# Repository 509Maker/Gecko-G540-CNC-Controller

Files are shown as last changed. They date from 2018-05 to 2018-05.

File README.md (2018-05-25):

# Gecko G540 CNC Controller
***
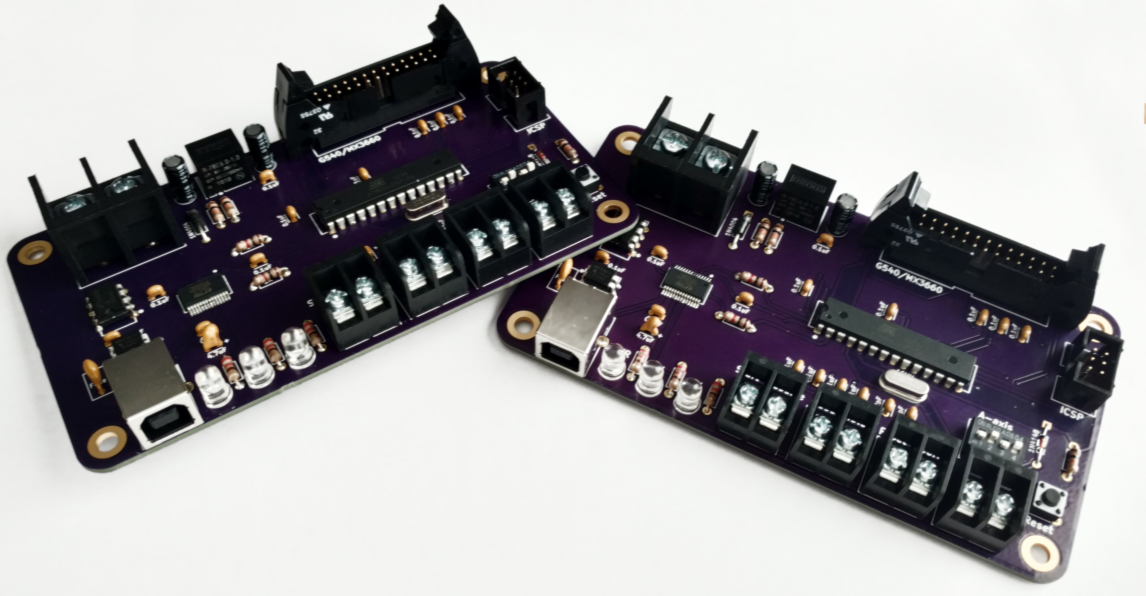
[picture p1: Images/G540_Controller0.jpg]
G540 Controller


#### Don’t be held back by a parallel port!

***

509Maker’s G540 USB CNC Controller is designed to be a plug and play solution for your G540 driver when using the GRBL or Estlcam firmware. 

* [GRBL](https://github.com/gnea/grbl) : Grbl is free software, released under the GPLv3 license.
* [Estlcam](https://www.estlcam.de/) : Affordable Windows Cam / Control software.

***
## Controller Overview

* Compatable with Estlcam and GRBL Latest releases.
* [custom Optiboot Bootloader](https://github.com/509Maker/Optiboot-for-grbl) : that disables D13 from toggling during a power cycle. 
* Authentic FTDI FT232RL USB bridge
* Atmega328P core processor
* ICSP header for atmega328p
* IDC26 header for direct connection to Gecko G540 driver
* Screw terminals for Start/Resume , Feed/Hold , Reset/Abort and Mist Coolant (Pin A4)
* On board dip switch to select what axis gecko clones on A-axis (X or Y)
* Power , RX and TX on board LED status indicators
* On board 5v 1A Recom regulator
* Board can be powered over USB or external source
* 7-24V External power source input screw terminals
* Limit switches , touch probe , spindle and coolant relays make full use of Opto-isolators through the Gecko built in G540 break out board.

The G540 usb CNC Controller when running the latest revision of GRBL is compatible with a number of cross platform control software. Such as GRBL Panel, Bcnc, universal G-code Sender just to name a few!

* [Bcnc](https://github.com/vlachoudis/bCNC) 
* [UGS](https://winder.github.io/ugs_website/) 
* [GRBL Panel](https://github.com/gerritv/Grbl-Panel) 

***

### Required GRBL Complie Time Options

* #define ENABLE_M7  By Uncommenting this line you can use the additinal onboard output labeled A4 for Mist Coolant. 
* #define USE_SPINDLE_DIR_AS_ENABLE_PIN This will need to be uncommented due to the controllers IDC26 Header pinout. 

As you will see in the grbl config.h file the defualt behavior of Optiboot to toggle pin D13 during a power cycle can cause issues ( unintentional spindle start). Please see above; as you will need to use our updated bootloader to rectify this potential problem. Like wise you can choose to not run a bootloader and load grbl via a programmer. It is reccomended to use the custom Optiboot bootloader to allow easy and quick updates over USB. 

***

### Best Way To Show Support For My Work

* [Shop On Amazon](https://amzn.to/2LtLY6S) : If you are in the U.S.A you can use my amazon affiliate link to do your regular amazon shoping at no additinal cost to you ! I recive a small amount when items are purchased through my link. 
* [Paypal Donations](https://www.paypal.com) : Can be sent to Contact@509maker.com
* [Blank PCB](https://www.509maker.com/product/pcb-cnc-controller/) : From time to time I will have blank cnc controller pcb's avalible in single quantity. Boards are made by Oshpark. When you only need one board and want to support the designer it is a great choice. 

# Thank You

No matter how you support my work, from any of the above to sharing your builds and projects with me and on social media platforms. Thank you ! I appreciate it. 

***

### License 

CC BY-NC 4.0

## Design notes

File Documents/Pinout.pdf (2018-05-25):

LPT IDC26 / DB25 | CONNECTION | IMPLEMENTED USE
1 | Output | Spindle On / Off Signal
2 | X-axis Step
3 | X-axis Dir
4 | Y-axis Step
5 | Y-axis Dir
6 | Z-axis Step
7 | Z-axis Dir
8 | A-axis Step | Clone Y-axis Step
9 | A-axis Dir | Clone Y-axis Dir
10 | Input | X-axis Limit/Home Switch Signal
11 | Input | Y-axis Limit/Home Switch Signal
12 | Input | Z-axis Limit/Home Switch Signal
13 | Input | Tool Probe / Touch Off Plate Signal
14 | PWM | Spindle Speed PWM Signal
15 | Not Used
16 | Not Used
17 | Output | Coolant On / Off Signal
18 | GND
19 | GND
20 | GND
21 | GND
22 | GND
23 | GND
24 | GND
25 | GND
26 | Not Used

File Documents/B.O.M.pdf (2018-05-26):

# Gecko G540 CNC Controller B.O.M

Quantity | Part | Digikey Source | Digikey Price | Amazon Option
1 | ATMEGA328P-PU | ATMEGA328P-PU-ND (https://www.digikey.com/product-detail/en/microchip-technology/ATMEGA328P-PU/ATMEGA328P-PU-ND/1914589) | $2.14 | ATMEGA328P (https://amzn.to/2xfAS1Z)
1 | FT232RL-REEL | 768-1007-1-ND (https://www.digikey.com/product-detail/en/ftdi-future-technology-devices-international-ltd/FT232RL-REEL/768-1007-1-ND/1836402) | $4.50
1 | LM358AN | LM358ANFS-ND (https://www.digikey.com/product-detail/en/on-semiconductor/LM358AN/LM358ANFS-ND/458690) | $0.50 | LM358AN (https://amzn.to/2KY8kw6)
1 | IRFD9014PBF | IRFD9014PBF-ND (https://www.digikey.com/product-detail/en/vishay-siliconix/IRFD9014PBF/IRFD9014PBF-ND/812475) | $1.02 | IRFD9014PBF (https://amzn.to/2LtWfjc)
1 | USB-B1HSB6 | ED2983-ND (https://www.digikey.com/product-detail/en/on-shore-technology-inc/USB-B1HSB6/ED2983-ND/2677744) | $0.58 | USB-B (https://amzn.to/2J8uOxa)
1 | XG4A-2632 | OR1094-ND (https://www.digikey.com/product-detail/en/omron-electronics-inc-emc-div/XG4A-2632/OR1094-ND/1829320) | $1.70 | XG4A-2632 (https://amzn.to/2IQoxXq)
1 | 30306-6002HB | 3M15451-ND (https://www.digikey.com/product-detail/en/3m/30306-6002HB/3M15451-ND/1237391) | $0.64 | IDC-Header (https://amzn.to/2LtSCK9)
1 | OSTYK55102030 | ED2926-ND (https://www.digikey.com/product-detail/en/on-shore-technology-inc/OSTYK55102030/ED2926-ND/2605215) | $1.34
4 | OSTYK22102030 | ED2958-ND (https://www.digikey.com/product-detail/en/on-shore-technology-inc/OSTYK22102030/ED2958-ND/1588708) | $1.05 | Barrier-Block (https://amzn.to/2IPJa2a)
1 | 1825057-3 | 450-1364-ND (https://www.digikey.com/product-detail/en/te-connectivity-alcoswitch-switches/1825057-3/450-1364-ND/969174) | $0.88 | Dip-Switch (https://amzn.to/2LzqTIe)
1 | 1825910-6 | 450-1650-ND (https://www.digikey.com/product-detail/en/te-connectivity-alcoswitch-switches/1825910-6/450-1650-ND/1632536) | $0.10 | 1825910-6 (https://amzn.to/2LyTRI8)
1 | ATS16A-E | CTX1084-ND (https://www.digikey.com/product-detail/en/cts-frequency-controls/ATS16A-E/CTX1084-ND/2640062) | $0.36 | 16MHz-Crystal (https://amzn.to/2J8Mrgb)
1 | R-78E5.0-1.0 | 945-2201-ND (https://www.digikey.com/product-detail/en/recom-power/R-78E5.0-1.0/945-2201-ND/4930585) | $3.26 | R-78E5.0-1.0 (https://amzn.to/2xf33hA)
1 | RHEF050 | RHEF050HF-ND (https://www.digikey.com/product-detail/en/littelfuse-inc/RHEF050/RHEF050HF-ND/5130260) | $0.55 | Fuse (https://amzn.to/2GRt9qL)
2 | UKL1H100KDDANA | UKL1H100KDDANA-ND (https://www.digikey.com/product-detail/en/nichicon/UKL1H100KDDANA/UKL1H100KDDANA-ND/2428102) | $0.50 | UKL1H100KDDANA (https://amzn.to/2KXuiPS)
1 | C503B-RCN-CW0Z0AA1 | C503B-RCN-CW0Z0AA1-ND (https://www.digikey.com/product-detail/en/cree-inc/C503B-RCN-CW0Z0AA1/C503B-RCN-CW0Z0AA1-ND/1922930) | $0.15 | Red-Led (https://amzn.to/2IQrRBS)
1 | C503B-GAN-CB0F0791 | C503B-GAN-CB0F0791-ND (https://www.digikey.com/product-detail/en/cree-inc/C503B-GAN-CB0F0791/C503B-GAN-CB0F0791-ND/1922938) | $0.24 | Green-Led (https://amzn.to/2KZ4McP)
1 | C503B-AAN-CY0B0251 | C503B-AAN-CY0B0251-ND (https://www.digikey.com/product-detail/en/cree-inc/C503B-AAN-CY0B0251/C503B-AAN-CY0B0251-ND/1922932) | $0.15 | Amber-Led (https://amzn.to/2kr9kxB)
3 | CF14JT220R | CF14JT220RCT-ND (https://www.digikey.com/product-detail/en/stackpole-electronics-inc/CF14JT220R/CF14JT220RCT-ND/1830334) | $0.10 | CF14JT220R (https://amzn.to/2IQgo5p)
3 | CF14JT10K0 | CF14JT10K0CT-ND (https://www.digikey.com/product-detail/en/stackpole-electronics-inc/CF14JT10K0/CF14JT10K0CT-ND/1830374) | $0.10 | CF14JT10K0 (https://amzn.to/2ktRIBk)
2 | CF14JT1K00 | CF14JT1K00CT-ND (https://www.digikey.com/product-detail/en/stackpole-electronics-inc/CF14JT1K00/CF14JT1K00CT-ND/1830350) | $0.10 | CF14JT1K00 (https://amzn.to/2J4WRh7)
14 | C320C104K5R5TA | 399-4264-ND (https://www.digikey.com/product-detail/en/kemet/C320C104K5R5TA/399-4264-ND/818040) | $0.22 | C320C104K5R5TA (https://amzn.to/2ILOR5b)
2 | C315C220K5G5TA | 399-9723-ND (https://www.digikey.com/product-detail/en/kemet/C315C220K5G5TA/399-9723-ND/3726119) | $0.37 | 22pF-Cap (https://amzn.to/2J4ZrUa)
1 | 1N4148 | 1N4148FS-ND (https://www.digikey.com/product-detail/en/on-semiconductor/1N4148/1N4148FS-ND/458603) | $0.10 | 1N4148 (https://amzn.to/2xewEb3)
1 | 1N4004-T | 1N4004DICT-ND (https://www.digikey.com/product-detail/en/diodes-incorporated/1N4004-T/1N4004DICT-ND/160593) | $0.14 | 1N4004-T (https://amzn.to/2GSxnhy)
1 | 199D475X9016B1V1E3 | 718-1220-ND (https://www.digikey.com/product-detail/en/vishay-sprague/199D475X9016B1V1E3/718-1220-ND/1559859) | $1.04 | 199D475X9016B1V1E3 (https://amzn.to/2Ja3XAN)
Quantity | Part | Source
1 | Blank PCB | 509Maker.com (https://www.509maker.com/product/pcb-cnc-controller/)

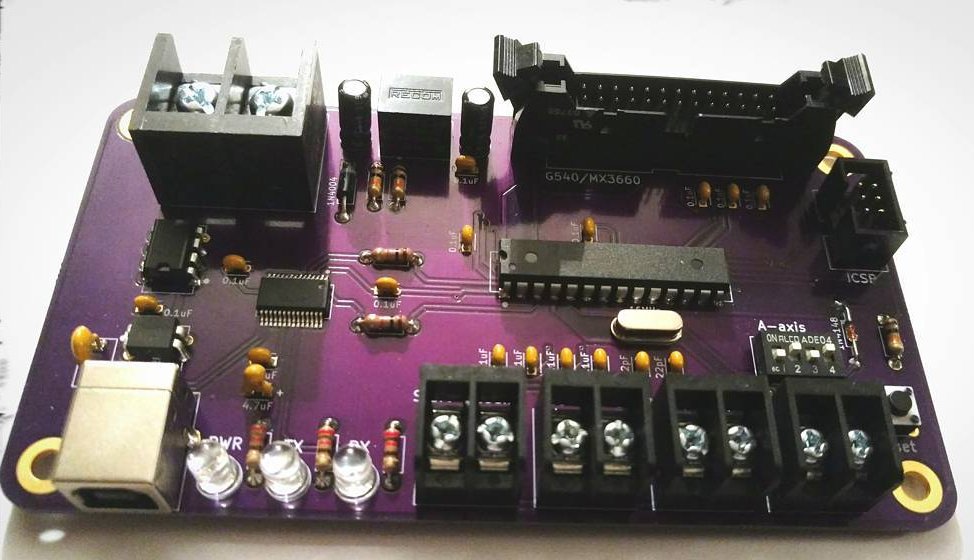
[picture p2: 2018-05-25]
Images/G540_Controller1.jpg

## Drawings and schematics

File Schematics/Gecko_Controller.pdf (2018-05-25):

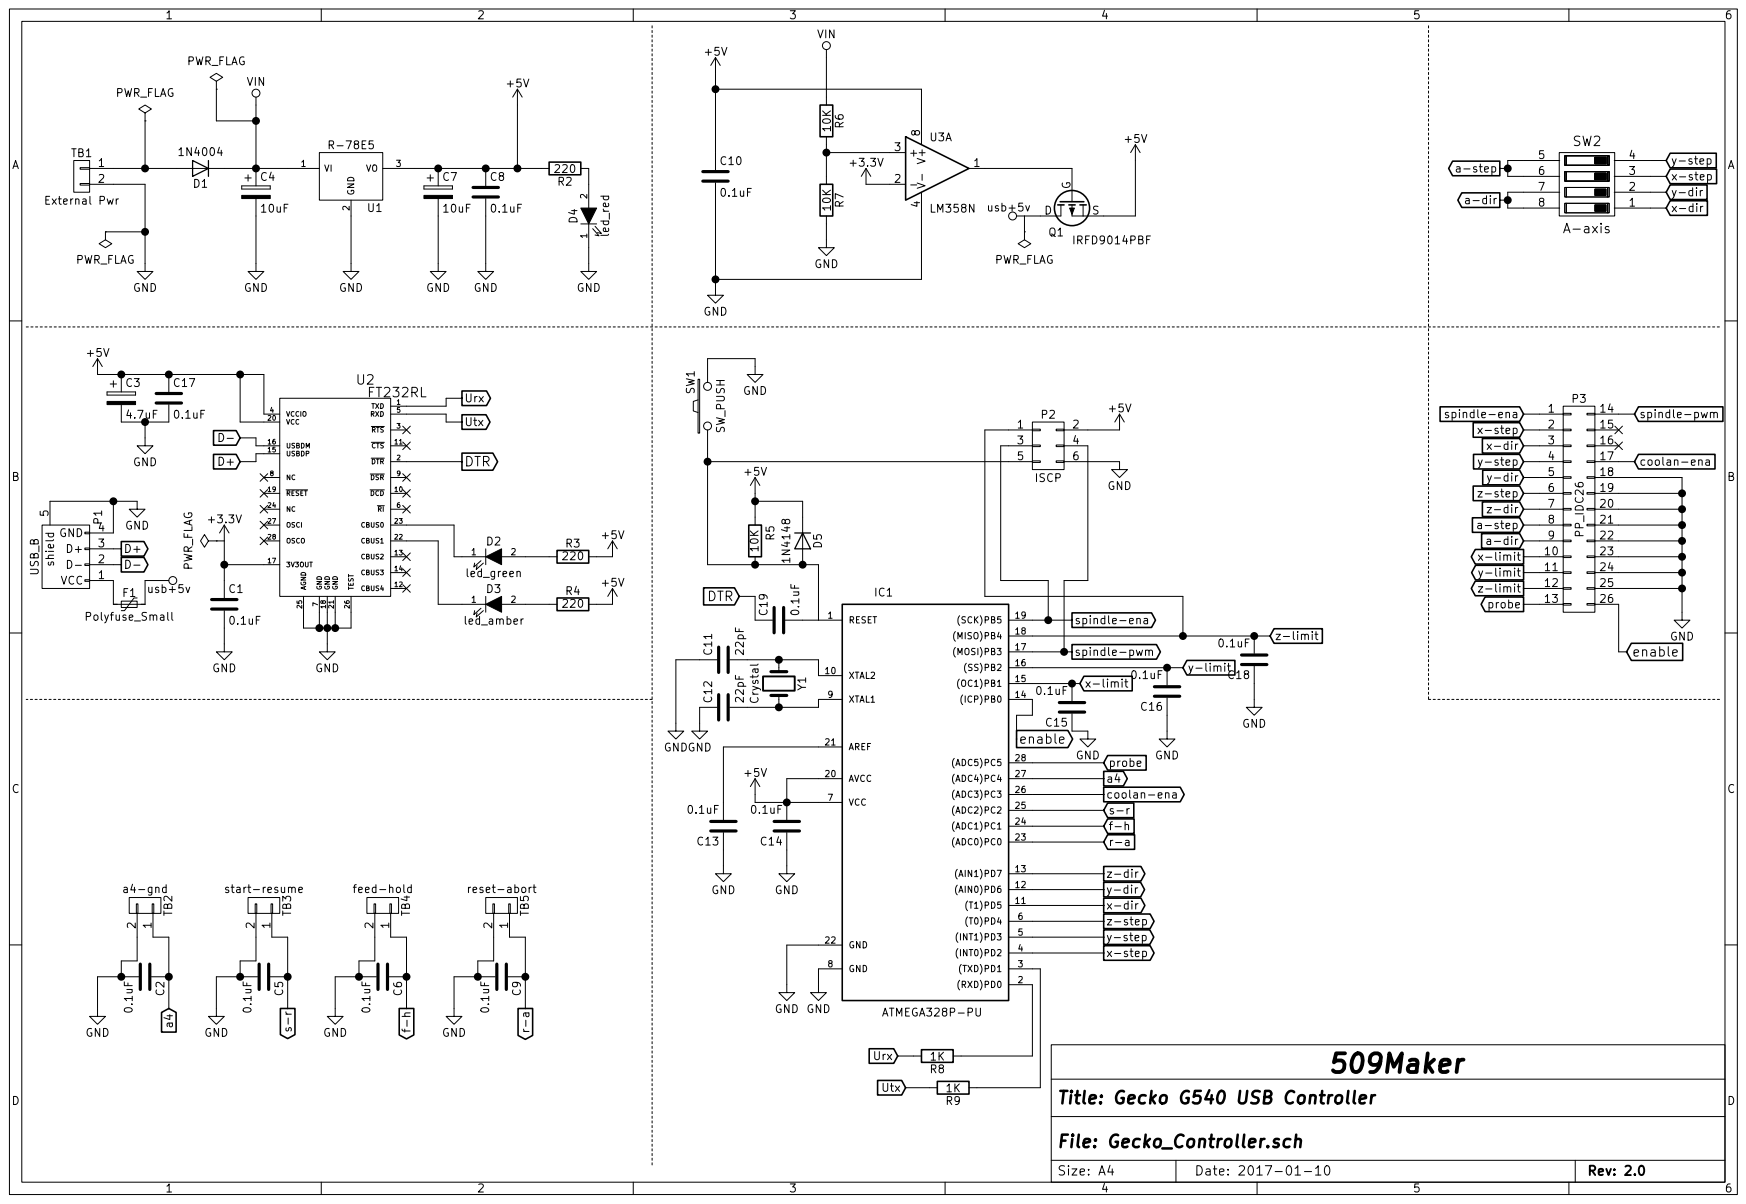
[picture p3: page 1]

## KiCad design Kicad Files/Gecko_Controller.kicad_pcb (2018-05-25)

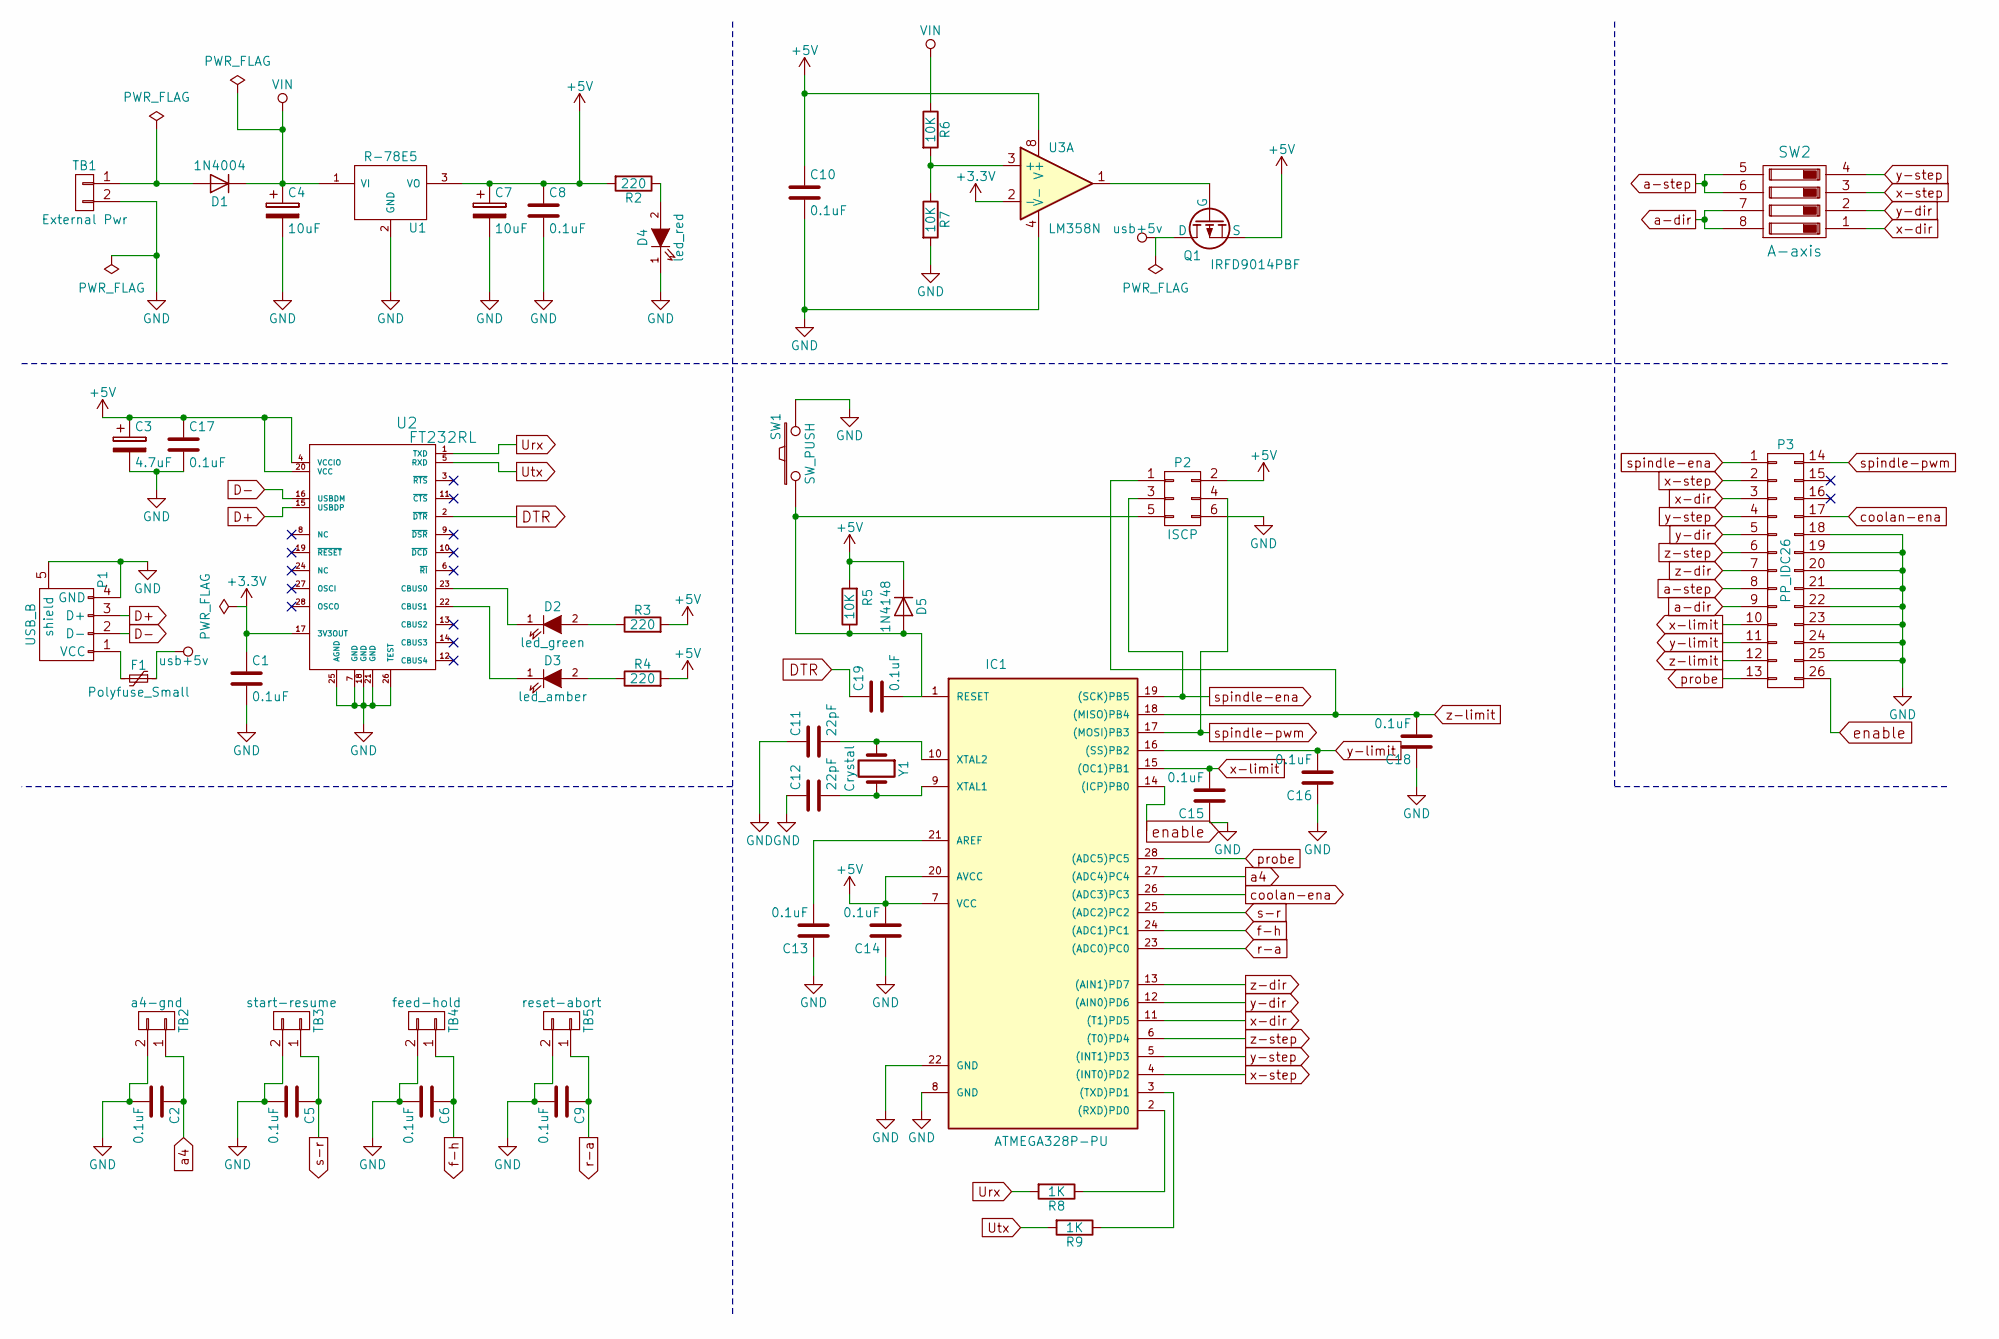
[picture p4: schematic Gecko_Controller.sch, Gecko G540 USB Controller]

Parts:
C1, C2, C5, C6, C8, C9, C10, C13, C14, C15, C16, C17, C18, C19: 0.1uF; C_Disc_D3_P2.5
C3: 4.7uF; C_Radial_D5_L11_P2.5
C4, C7: 10uF; C_Radial_D5_L11_P2
C11, C12: 22pF; C_Disc_D3_P2.5
D1: 1N4004; Diode_DO-41_SOD81_Horizontal_RM10
D2: led_green; LED-5MM
D3: led_amber; LED-5MM
D4: led_red; LED-5MM
D5: 1N4148; Diode_DO-35_SOD27_Horizontal_RM10
F1: Polyfuse_Small; C_Disc_D7.5_P5
IC1: ATMEGA328P-PU; DIP-28_W7.62mm
P1: USB_B
P2: ISCP; vasch_strip_3x2
P3: PP_IDC26; IDC_Header_LPT_Pinout_26pins
Q1: IRFD9014PBF; DIP-4_W7.62mm
R2, R3, R4: 220; Resistor_Horizontal_RM7mm
R5, R6, R7: 10K; Resistor_Horizontal_RM7mm
R8, R9: 1K; Resistor_Horizontal_RM7mm
SW1: SW_PUSH; SW_PUSH_6mm
SW2: A-axis; dip_4-300
TB1: External Pwr; OSTYK55102030
TB2: a4-gnd; OSTYK22102030
TB3: start-resume; OSTYK22102030
TB4: feed-hold; OSTYK22102030
TB5: reset-abort; OSTYK22102030
U1: R-78E5; R-78E5_TO-220
U2: FT232RL; SSOP-28_5.3x10.2mm_Pitch0.65mm
U3: LM358N; DIP-8_W7.62mm
Y1: Crystal; HC-49V

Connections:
+3V3: C1.1, U2.17 (3V3OUT), U3.2 (-)
+5V: C3.1, C7.1, C8.1, C10.1, C14.2, C17.1, D5.1 (K), IC1.7 (VCC), IC1.20 (AVCC), P2.2, Q1.4 (S), R2.2, R3.2, R4.2, R5.2, U1.3 (VO), U2.4 (VCCIO), U2.20 (VCC), U3.8 (V+)
D+: P1.3 (D+), U2.15 (USBDP)
D-: P1.2 (D-), U2.16 (USBDM)
DTR: C19.1, U2.2 (~DTR)
GND: C1.2, C2.2, C3.2, C4.2, C5.2, C6.2, C7.2, C8.2, C9.2, C10.2, C11.1, C12.1, C13.1, C14.1, C15.1, C16.1, C17.2, C18.1, D4.1 (K), IC1.8 (GND), IC1.22 (GND), P1.4 (GND), P1.5 (shield), P2.6, P3.18, P3.19, P3.20, P3.21, P3.22, P3.23, P3.24, P3.25, R7.2, SW1.2, TB1.2, TB2.2, TB3.2, TB4.2, TB5.2, U1.2 (GND), U2.7 (GND), U2.18 (GND), U2.21 (GND), U2.25 (AGND), U2.26 (TEST), U3.4 (V-)
unnamed: C11.2, IC1.10 (XTAL2), Y1.1
unnamed: C12.2, IC1.9 (XTAL1), Y1.2
unnamed: C13.2, IC1.21 (AREF)
unnamed: C19.2, D5.2 (A), IC1.1 (RESET), P2.5, R5.1, SW1.1
unnamed: D1.2 (A), TB1.1
unnamed: D2.1 (K), U2.23 (CBUS0)
unnamed: D2.2 (A), R3.1
unnamed: D3.1 (K), U2.22 (CBUS1)
unnamed: D3.2 (A), R4.1
unnamed: D4.2 (A), R2.1
unnamed: F1.2, P1.1 (VCC)
unnamed: IC1.2 ((RXD)PD0), R8.1
unnamed: IC1.3 ((TXD)PD1), R9.1
unnamed: Q1.3 (G), U3.1
unnamed: R6.2, R7.1, U3.3 (+)
Urx: R8.2, U2.1 (TXD)
Utx: R9.2, U2.5 (RXD)
VIN: C4.1, D1.1 (K), R6.1, U1.1 (VI)
a4: C2.1, IC1.27 ((ADC4)PC4), TB2.1
a-dir: P3.9, SW2.7, SW2.8
a-step: P3.8, SW2.5, SW2.6
coolan-ena: IC1.26 ((ADC3)PC3), P3.17
enable: IC1.14 ((ICP)PB0), P3.26
f-h: C6.1, IC1.24 ((ADC1)PC1), TB4.1
probe: IC1.28 ((ADC5)PC5), P3.13
r-a: C9.1, IC1.23 ((ADC0)PC0), TB5.1
s-r: C5.1, IC1.25 ((ADC2)PC2), TB3.1
spindle-ena: IC1.19 ((SCK)PB5), P2.3, P3.1
spindle-pwm: IC1.17 ((MOSI)PB3), P2.4, P3.14
usb+5v: F1.1, Q1.1 (D)
x-dir: IC1.11 ((T1)PD5), P3.3, SW2.1
x-limit: C15.2, IC1.15 ((OC1)PB1), P3.10
x-step: IC1.4 ((INT0)PD2), P3.2, SW2.3
y-dir: IC1.12 ((AIN0)PD6), P3.5, SW2.2
y-limit: C16.2, IC1.16 ((SS)PB2), P3.11
y-step: IC1.5 ((INT1)PD3), P3.4, SW2.4
z-dir: IC1.13 ((AIN1)PD7), P3.7
z-limit: C18.2, IC1.18 ((MISO)PB4), P2.1, P3.12
z-step: IC1.6 ((T0)PD4), P3.6

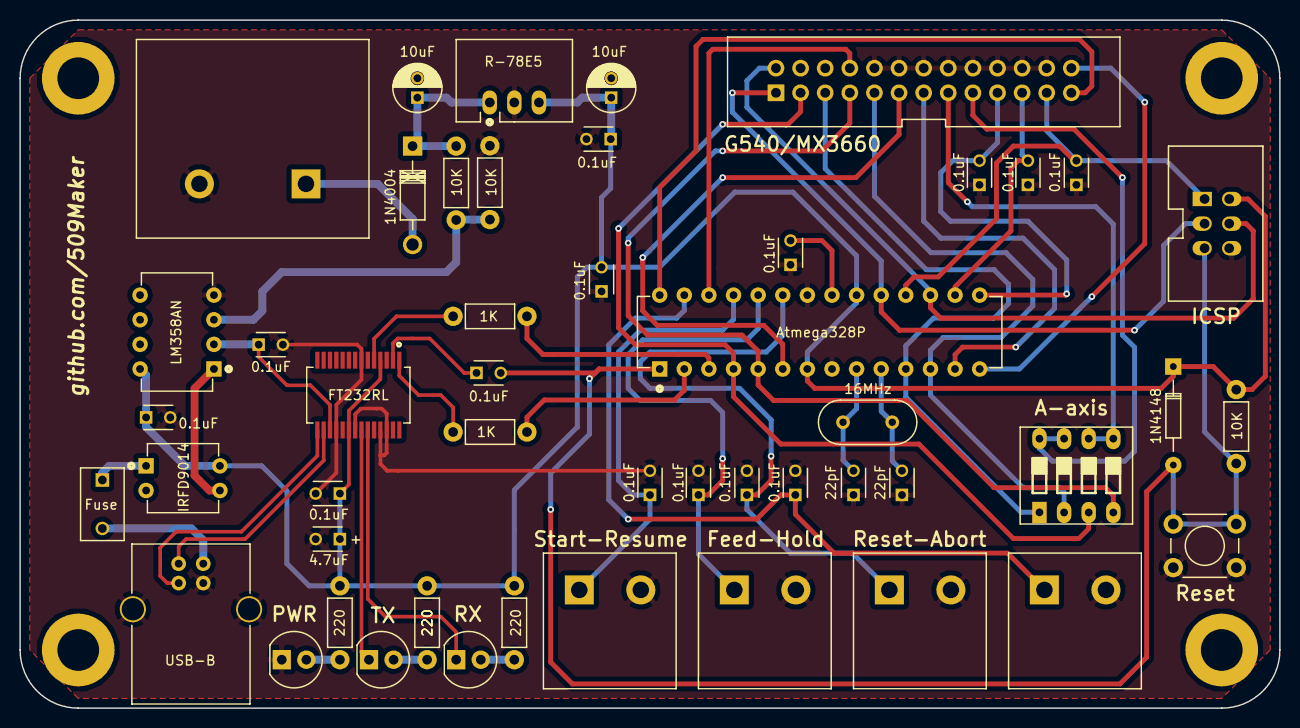
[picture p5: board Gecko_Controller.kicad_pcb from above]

Board: 2 copper layers, 130.0 x 71.0 mm, 49 parts (0 on the bottom side), 45 nets.

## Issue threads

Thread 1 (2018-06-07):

(Not an issue) Thanks for the board!

tt2468, 2018-06-07:
I just wanted to say thank you 509Maker for designing this board! I ordered a blank PCB and all of the parts off DigiKey, so I'm just waiting for them to arrive.

I'm totally new to grbl and CNC, so it took some time to understand the readme. I would suggest linking the grbl build instructions in the readme and clarifying which steps need to be done depending on the firmware upload route (compiling grbl w/o optiboot vs uploading with the custom optiboot)

I also rebuilt optiboot myself with what appears to be the latest changes, so I'll post an update on if my build worked or not.

But yeah thanks a ton for designing this board! I think it's way better than a ll the other grbl g540 breakout boards.
